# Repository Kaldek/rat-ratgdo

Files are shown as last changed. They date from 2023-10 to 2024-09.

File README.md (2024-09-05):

# rat-ratgdo
RAGE
AGAINST
THE
RATGDO



Credit and inspiration for this work goes to [@rlowens](https://github.com/rlowens) to let me know that there are other technical folks out there who needed this other than myself.

## Overview
This is an open source schematic for the ratgdo, based on the v2.5 [ratgdo](https://github.com/PaulWieland/ratgdo) PCB and code but installed using the [ESPHome fork](ESPHome%20vs%20native%20ratgdo.md) of ratgdo.  This project was created to allow people who need a ratgdo solution for their garage door opener but either cannot, or choose not to, source the solution from Paul Wieland. It also ensures that the PCB can be recreated as and when the project maintainer gives up on the project (much like Chamberlain themselves might do with their MyQ Cloud Service) and stops selling PCBs. 

### You are expected to know how to create the described circuit using your own prototyping skills.  That is, this project is for people who can solder well and know how to read schematics

The ***basic*** PCB schematic shown here in the Readme does not describe any circuitry other than the serial line garage door control and obstruction sensor.  All other optional features provided by ratgdo can be reverse engineered as needed, or may already be solved by one of the schematics the community has uploaded!

 As of January 2023, there are now multiple sources for commercially sold ratgdo boards.  **However if you want to buy a pre-made ratgdo setup, we recommend purchasing one [from Paul Wieland](https://github.com/PaulWieland/ratgdo) so as to reward the original creator.**

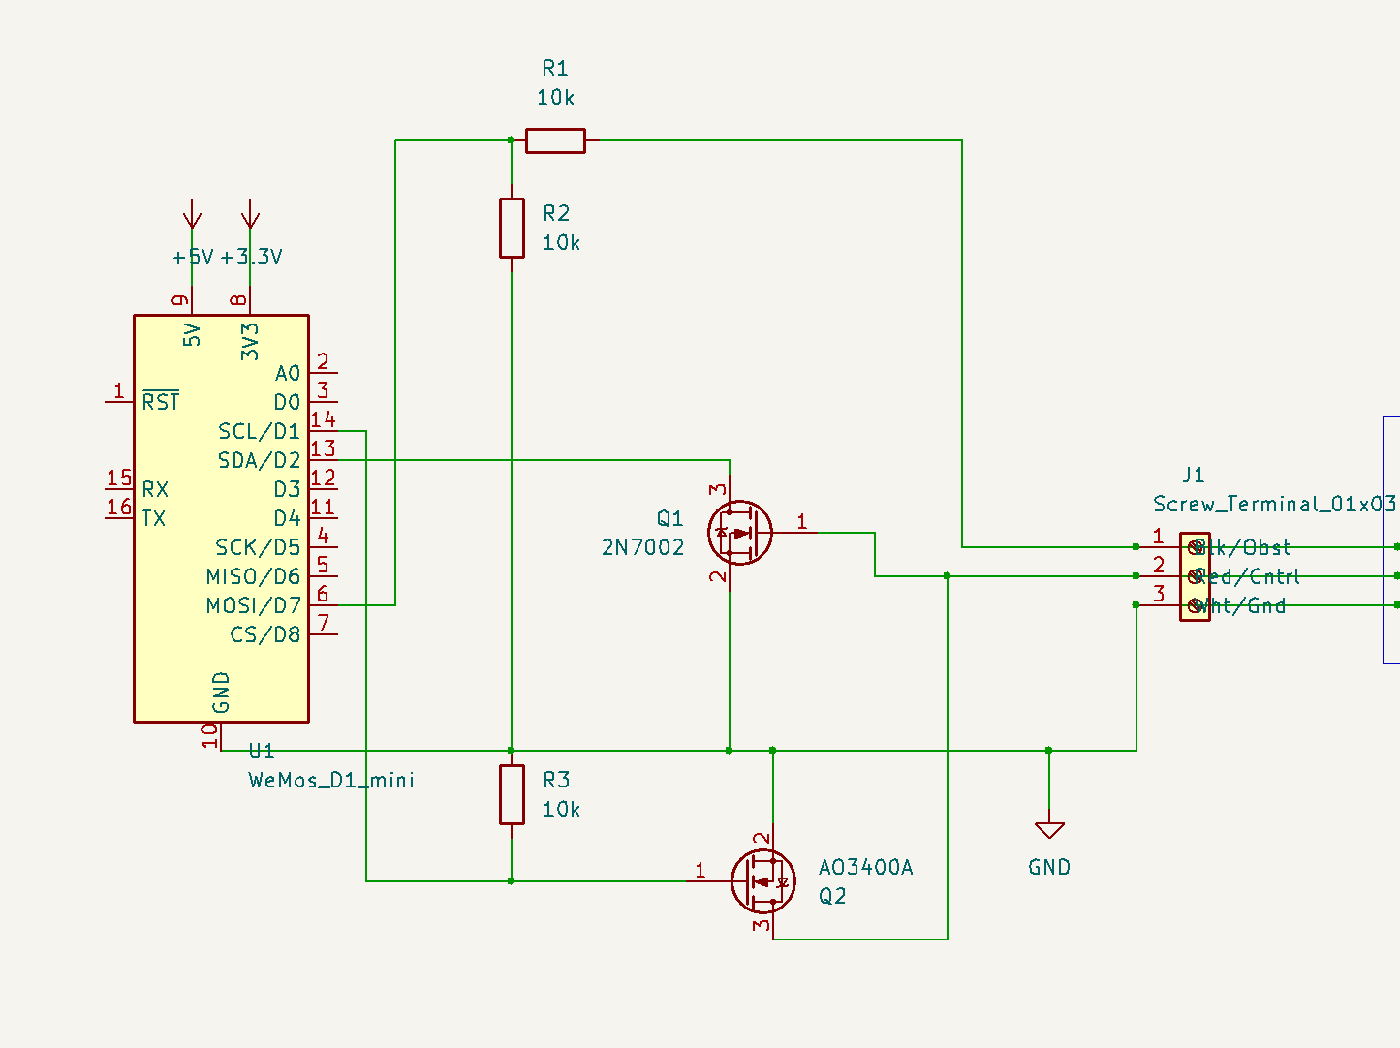
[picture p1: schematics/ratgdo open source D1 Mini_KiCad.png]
PCB Link

_Simple basic schematic for a Wemos D1 Mini based module_

See images of a [working breadboard prototype](images/Breadboard_working.png) and the [subsequent soldered prototype using a D1 shield](images/Simple%20prototype%20using%20D1%20shield.jpg).  Both of these prototypes are using 2n7000 MOSFETs exclusively, but that is because they are prototypes and whether a 2n7000 will work for TX will depend greatly on who manufactured your 2n7000.  See the section below on needed components for context.

## Components needed for basic functionality
The basic schematic shown above assumes the use of through-hole components.  If you wish to use SMD components, please refer to the [FAQ](FAQ.md#what-if-i-want-to-use-sot-23-smd-components), and you can also check out the community-provided schematics, which include SMD-based designs.

For this basic design, aside from the obvious requirement of a [supported ESP-32 or ESP8266 board](Supported%20Boards.md) flashed with the [ESPHome version](https://github.com/ratgdo/esphome-ratgdo), you will need:
- 3x 10 kohm (kilo-ohm) resistors
- 1x 2n7000 MOSFET for the RX pin
- 1x AO3400A (soldered to a SOT23 to DIP adapter board) for the TX pin.

It is also recommended you aquire a suitable 3-post screw terminal and some red, white, and black wire for connecting to the door opener.  These connections are very low current, so you can get away with fairly thin wire.

**Note:**  You may **try** to use a 2n7000 MOSFETs for **both** RX and TX, however depending on the manufacturere of your 2n7000 and its production batch, it might not be 100% reliable for the TX circuit because the ~3v switching signal from the ESP8266 may not be enough to trigger the gate of the 2n7000.  There are many examples working using the 2n7000 however, so it might work.  If you have reliability issues for sending commands, we can only recommend you use the AO3400A SMD MOSFET, soldered to a SOT23-to-DIP adapter board.  

## INSTALL REQUIREMENTS
For both this basic schematic shown here in the Readme and how they it is laid out, you must use the ESPHome fork of ratgdo and - for ESP8266 based boards - select the "ratgdo v2.5x" image on the ESPhome [web installer page](https://ratgdo.github.io/esphome-ratgdo/).  For ESP32 based boards the above does not currently apply and you must use the v2.0 installer and follow our basic ESP-32 schematic we provide in the Supported Boards page.

For the ESP8266 based boards, if installing using Paul Wieland's native ratgdo installer and you install for a v2.0 board, you must wire your TX to D4 (GPIO2) rather than D1 (GPIO5).

## Having a PCB printed
You may use the files from the [schematics folder](kicad_files) to have your own PCB printed.  Shown is an example 3D render of an ESP32 based board using a Wemos ESP32 D1 board.

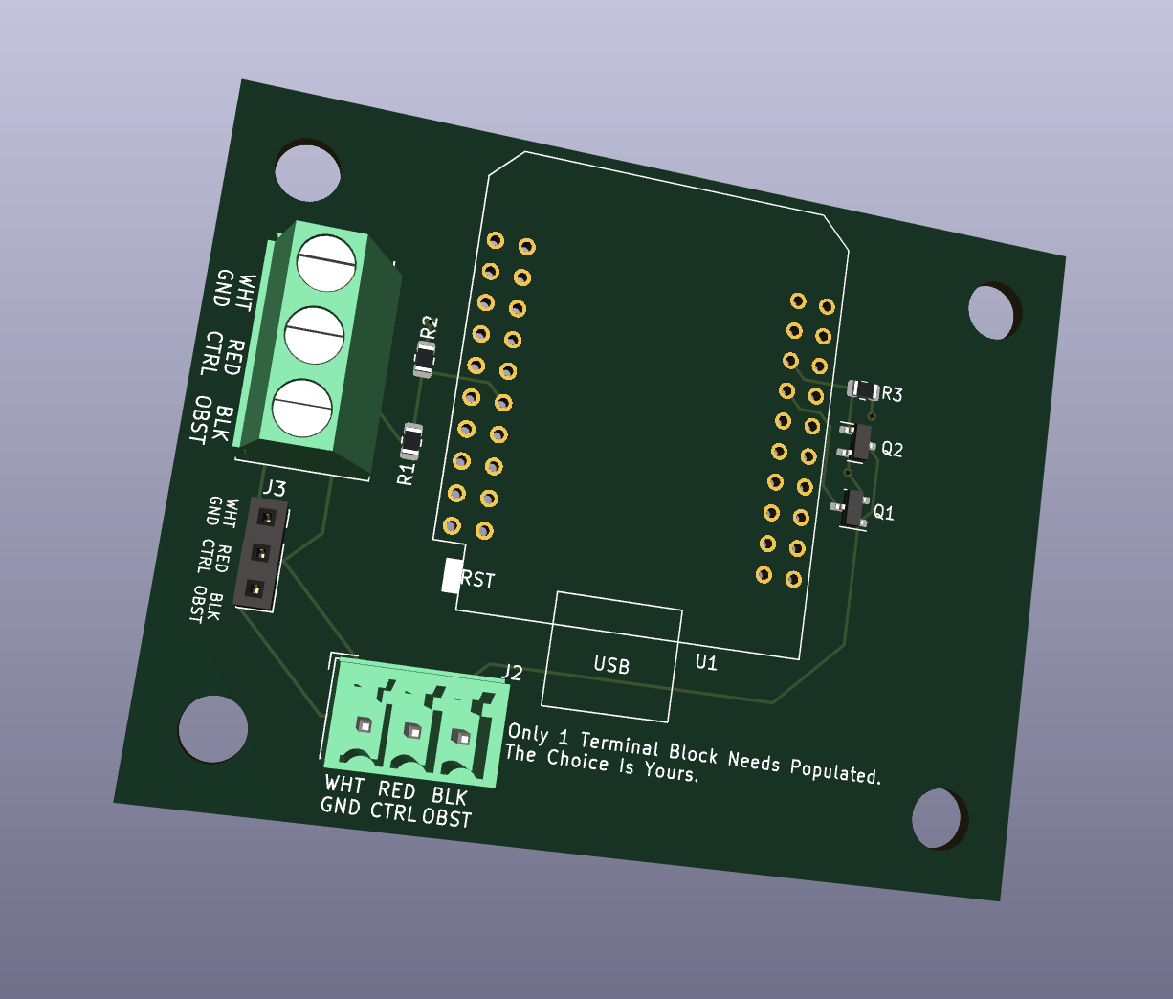
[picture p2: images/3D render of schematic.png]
3D render of printed PCB

_An example of the D1 Mini ESP32 Wide Format_

Here is an example of a printed PCB with a raw ESP8266 and an LM2596 module, for being powered by a GDO with the battery backup capabilities.
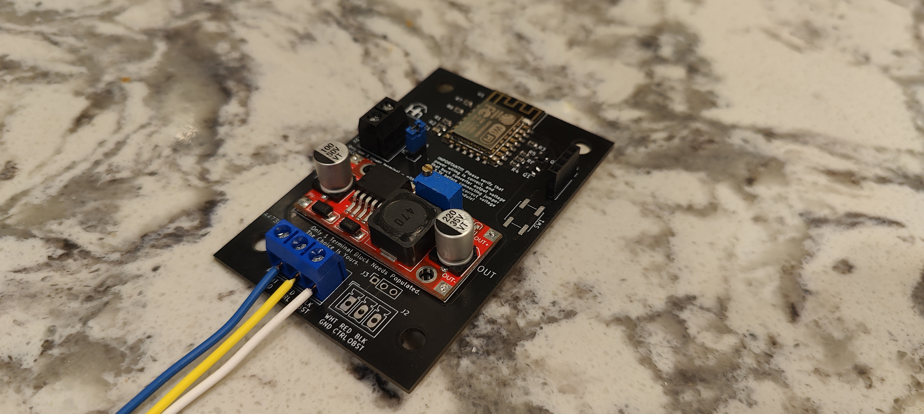
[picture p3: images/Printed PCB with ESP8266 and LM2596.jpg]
Printed PCB using ESP8266 and LM2596

_An example of a PCB using a bare ESP8266 and LM2596 module_

### Schematic options
The community has provided a few options of schematic files suitable for sending to a PCB printing company.
- [Wemos D1 Mini ESP8266](kicad_files/D1%20Mini%20-%20ESP8266)
- [Wemos D1 Mini ESP32](kicad_files/D1%20Mini%20-%20ESP32) (massive overkill for ratgdo but it's your choice!)
- [Wemos D1 Mini ESP32 Wide Format](kicad_files/D1%20Mini%20Wide%20-%20ESP32)
- [Bare ESP8266 module](kicad_files/Bare%20ESP8266)

> If you just want to try ordering a board from somewhere like PCBWay, then check out the most recent [build artifacts](https://github.com/Kaldek/rat-ratgdo/actions/workflows/pcb.yaml)

## How the ratgdo circuit works
The ratgdo circuitry which we cover in this project consists of two sections; Garage Door control and obstruction sensors.

### Garage Door Control
#### Description of the Chamberlain configuration
The Chamberlain garage door control circuit is a two-wire setup consisting of a Ground, and a combined +12v power and serial data line.  The serial data line is held at 12v unless data transmission is occurring.  Data transmission is performed by pulling the 12v line down to GND for each data bit.  The benefit here is that a single wire can be used for providing power to door control panels and data transmssion on a single wire.  The use of appropriately sized capacitors in door control panels means they do not switch off during data transmission.

#### How ratgdo interfaces with the Chamberlain wiring
The ratgdo taps into the red control wire and uses this single wire for transmission of commands onto the serial bus, and for receiving data from the serial bus.  As it is a single wire protocol and operates half-duplex, the ratgdo circuitry uses N-channel MOSFETs wired in a manner which allows the ESP8266 to never transmit when the serial line is already low.

In operation, this means that the ratgdo is mostly listening to the serial bus to ensure it is keeping track of the state of the door.  For example, if the door is manually opened (or opened by use of the MyQ app even), these events are broadcast onto the serial bus by the door controller.  ratgdo is therefore able to know that the state of the door has changed.  In turn, this means that when controlling ratgdo via Home Assistant, the status of the door in HA is always up to date.

#### Wiring to Garage Door


### Obstruction sensor
The ratgdo monitors the real-time state of the obstruction sensors directly.  We assume this is because obstruction status is not broadcast in real time by the door controller, and safety is paramount.  It allows you to set up real-time alerts in Home Assistant for any time the door is obstructed.  The ratgdo taps into the obstruction sensor power wire which also acts as a communication bus, however the signalling is only an ongoing status of whether the obstruction sensors are working and whether there is an obstruction.

## Contributing
This is a fully open repo, in that we welcome any and all additions for all sorts of Edge Cases.  If you come up with something and would like it to be available to the community, raise a Pull Request and we'll work with you to get it published!

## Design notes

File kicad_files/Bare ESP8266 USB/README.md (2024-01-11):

# ESP8266 12-F USB-C KiCad files

A reworking of the Bare ESP8266 board design that uses USB-C for power instead of an LM2596 submodule, and uses just one GDO connector header to allow for a smaller board footprint.

Compatable with RatGDO ESPHome software for the v2.5 official board.

## Populating

Populating the Flash switch, Reset switch, and ICSP header are optional, but will make first time programming easier.

## Powering 

This board uses a 6-pin power-only USB-C jack that can be either hand soldered or paste reflowed. It's a normal 5V USB sink device, so any "dumb" USB wall-wart can be used.

It can also be powered via the 3.3V pin of the ICSP header - there's no need to connect USB while serial programming it.

If you wish to power the device directly from the programming header using 3.3V, you can skip populating the USB-C port, resistors R2 and R3, and the LDO regulator CR1, but you should ensure you're using a stable and regulated 3.3V supply.

If your GDO has battery backup system, I'd recommend using one of the LM2996 module based boards in this repository instead of this one.

## Programming

The USB-C port on this board is for power only - you need to use the ICSP programming header with a seperate TTL-level RS232 programming interface to load the initial firmware.

The ICSP header will mate directly with the 
[SparkFun Serial Basic Breakout](https://www.sparkfun.com/products/14050) for programming, but any 3.3V RS232 interface can be used by connecting TX, RX, VCC and GND appropriately.

Auto reset via serial hardware control lines isn't supported - you'll need to press the Reset button manually after programming, or power cycle the device.

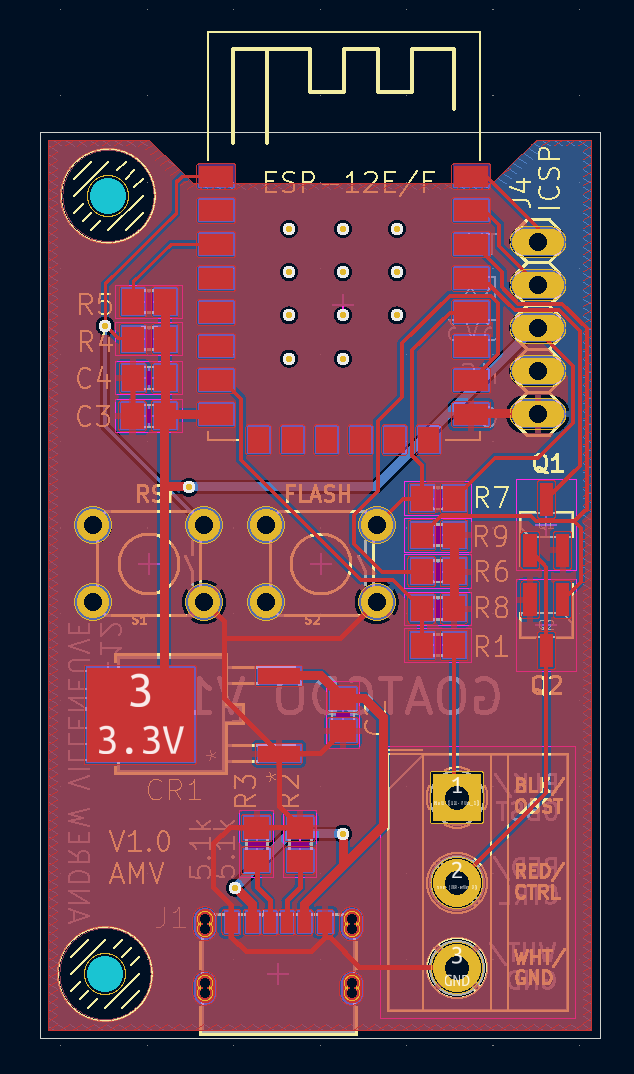
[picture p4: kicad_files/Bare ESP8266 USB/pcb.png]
KiCad Board View

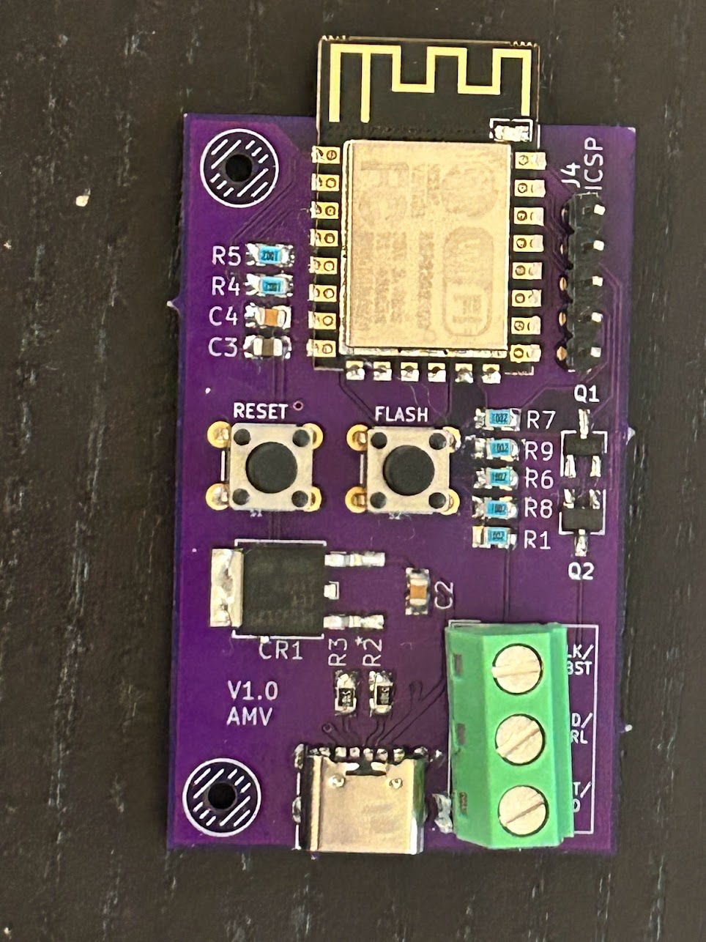
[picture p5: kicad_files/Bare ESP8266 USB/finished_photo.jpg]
Populated Board


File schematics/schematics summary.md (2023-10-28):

Place all schematic files and images here.

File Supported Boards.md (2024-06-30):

## ESP8266 D1 Mini boards
All ESP8266-based D1 Mini boards are supported, and are the hardware which the ratgdo project uses for the pre-made kits available from Paul Wieland.

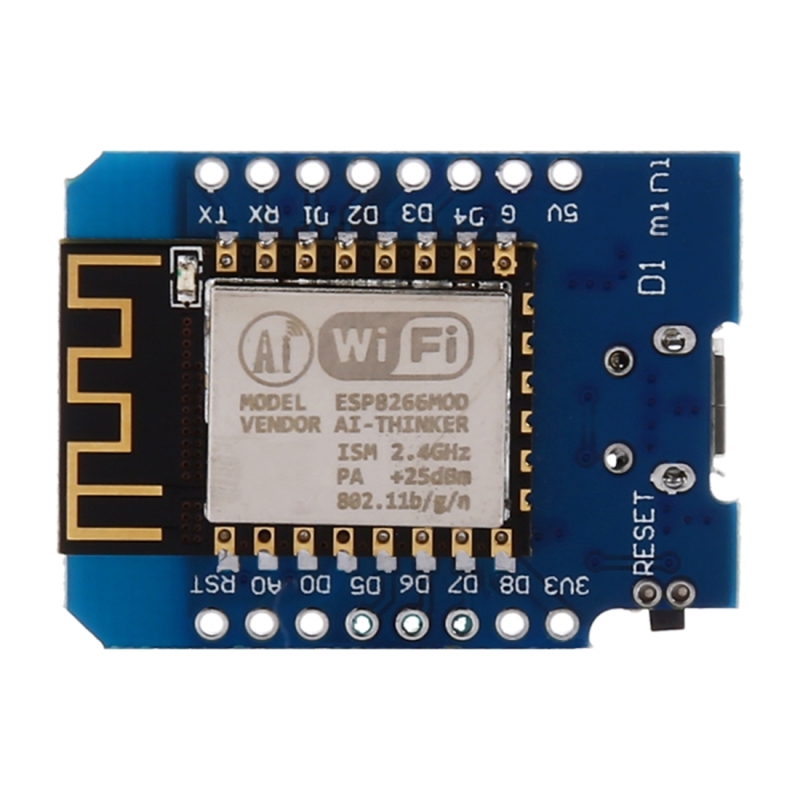
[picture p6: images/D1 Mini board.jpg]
D1 Mini Board


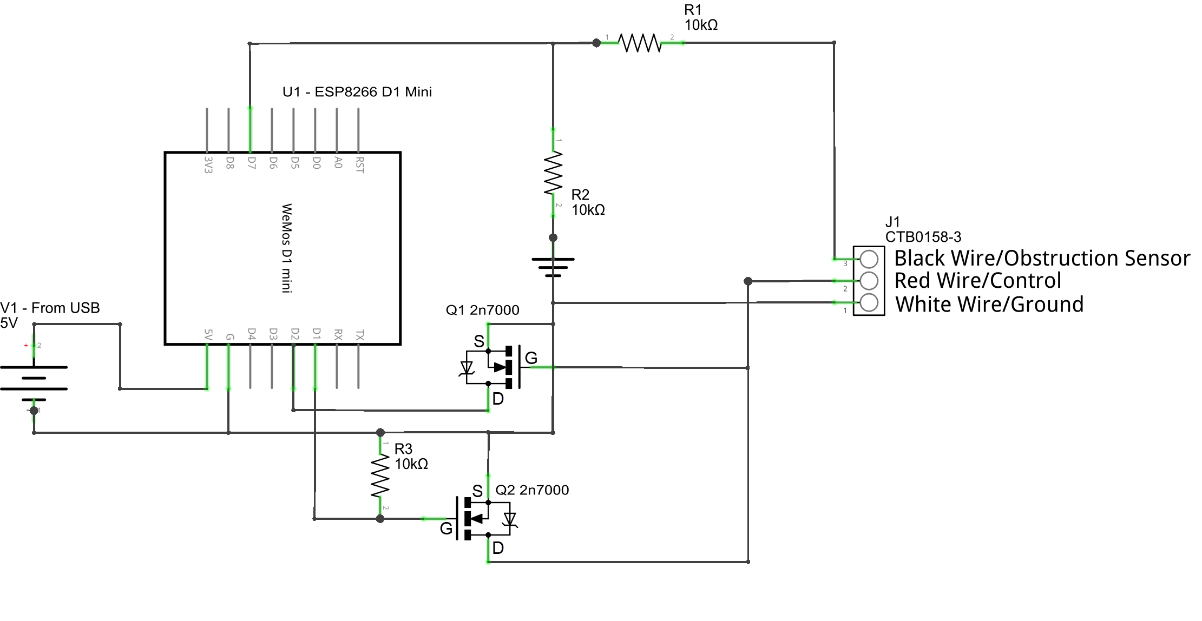
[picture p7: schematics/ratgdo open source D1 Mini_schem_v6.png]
ESP8266 D1 Mini Schematic


Note that the D1 Mini **module** takes 5v and an on-board regulator drops this down to the 3.3v power used by the ESP8266 chip.

## ESP-32 based boards
All ESP-32 boards are directly supported by the ESPHome Ratgdo port, using the [ESP32 D1 Mini YAML file for install settings for a version 2.0 ratgdo board](https://github.com/ratgdo/esphome-ratgdo/blob/main/static/v2board_esp32_d1_mini.yaml).

**CRITICAL**: You must install using the v2.0 install for ESP-32 boards as v2.5 is additional and unnecessary work for these boards at the current time.

**Note:** The pin numbers mentioned in the linked YAML file are only directly valid for the D1 Mini ESP32 boards.  Regardless of ESP-32 board used, these are the **actual** ESP-32 pins used for v2.0:
| ratgdo function | ESP-32 pin |
| --- | --- |
| TX | GPIO16 |
| RX | GPIO21 |
| Obstruction | GPIO23 |
| White/GND | GND |

For your particular board, you may need to determine which board traces map to these GPIO pins.

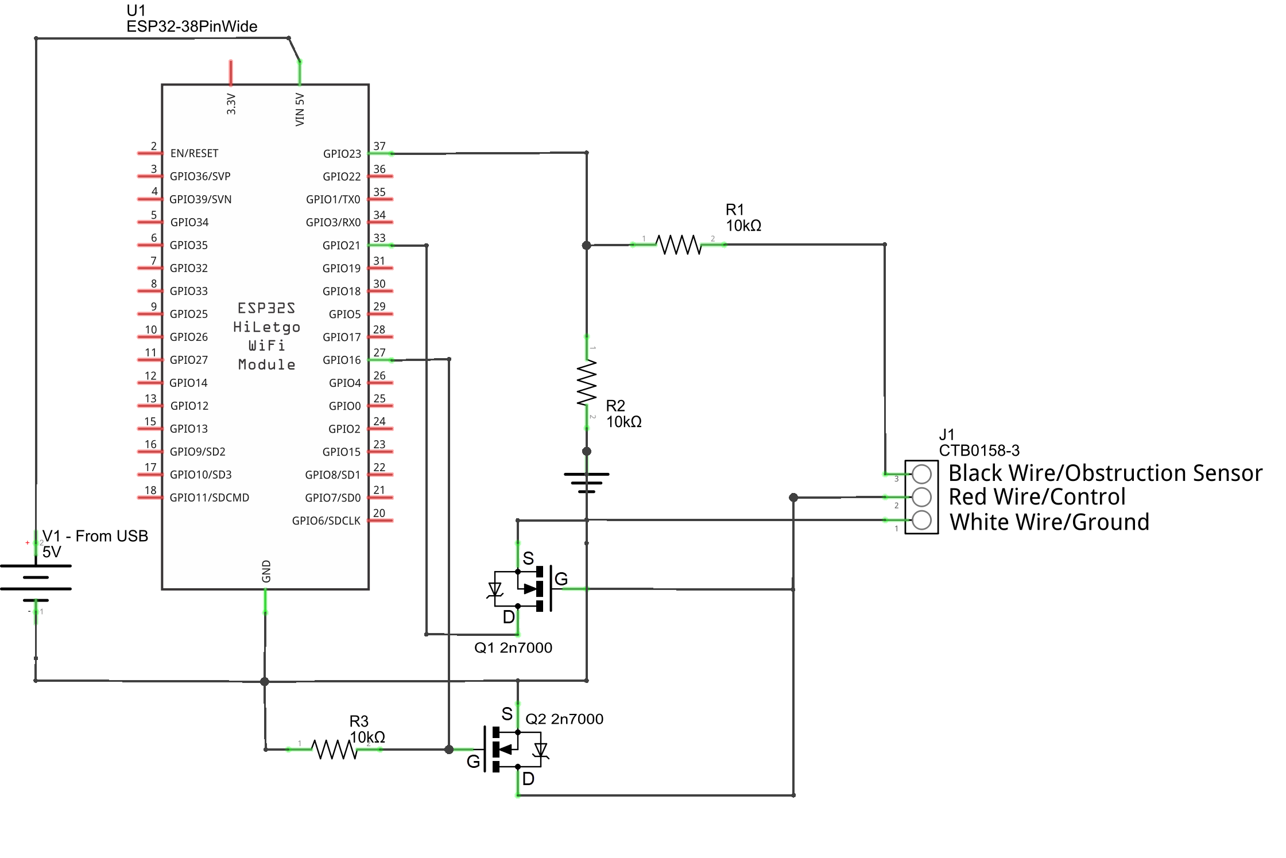
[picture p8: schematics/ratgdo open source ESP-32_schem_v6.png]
Generic ESP-32 board pinout


Note that ESP-32 **modules** take 5v power from USB and an on-board regulator drops this down to the 3.3v used by the ESP-32 chip.

### ESP-32 D1 Mini boards
Supported by the ESPHome Ratgdo port, using the ESP32 D1 Mini YAML file for install settings, noting thepinout mappings below..  Note that the outer row of pins on the D1 Mini board are not used for ratgdo.

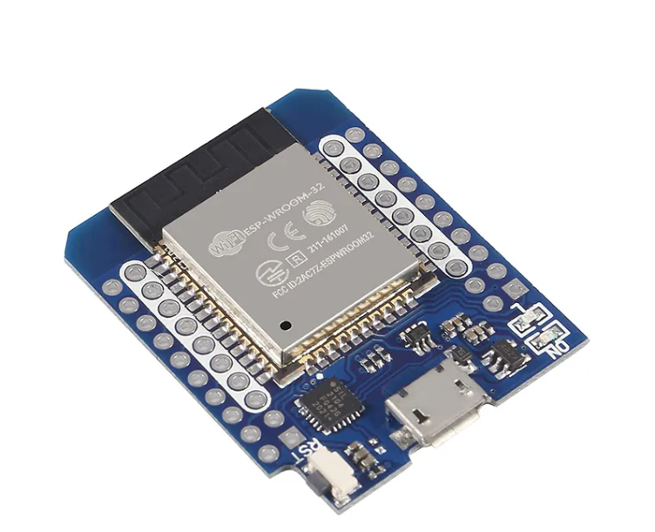
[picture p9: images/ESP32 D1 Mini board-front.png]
ESP-32 D1 Mini Front view

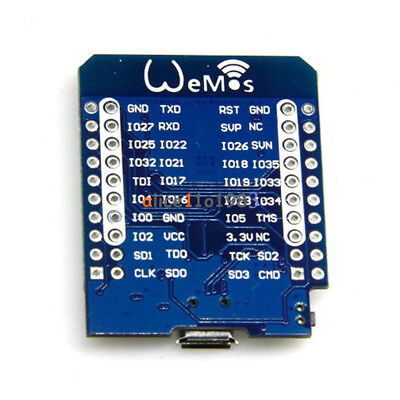
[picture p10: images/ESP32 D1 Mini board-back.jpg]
ESP-31 D1 Mini back view


GPIO pins for the ESP-32 D1 Mini are as follows:
- TX: IO16
- RX: IO21
- Obstruction: IO23

### ESP-WROOM-32
Supported by the ESPHome Ratgdo port, using the ESP32 D1 Mini YAML file for install settings, noting thepinout mappings below.

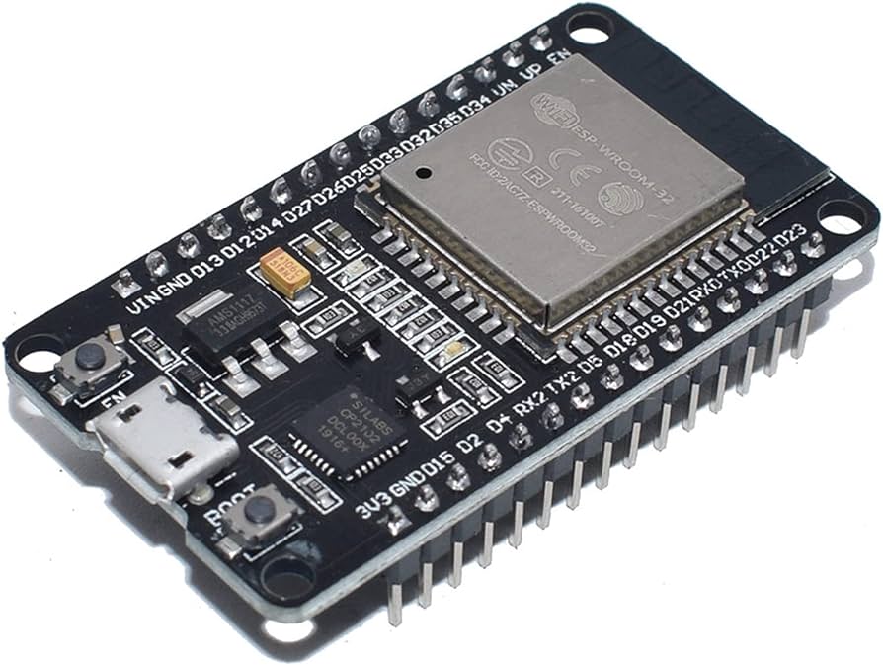
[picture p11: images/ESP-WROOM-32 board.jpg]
ESP-WROOM-32 board


GPIO pins for the ESP-WROOM-32 are as follows:
- TX: RX2
- RX: D21
- Obstruction: D23

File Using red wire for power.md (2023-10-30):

# Prototype notes for powering ESP module
We are testing use of an LM2596 voltage regulator (buck converter) module to power the ESP without needing a separate USB power supply.  

## Can we use the red wire to power the ESP?
Testing using this method has failed.  The LM2596 and ESP8266 combined draw too much current from the red wire for the ESP to be powered from the E-Serial lines of the Chamberlain/MyQ GDO. 

## Using the GDO Battery Backup connector to power the ratgdo
GDO models that are compatible with the Standby Battery Power System (e.g., the PN 475LM, [disassembly video](https://www.youtube.com/watch?v=qWsHb-kiO6w)) or have one built-in, can use the same 2-pin connector to power their LM2596 module.  Just be sure that you first adjust the output of your LM2596 voltage regulator to 5v **before** you connect it to your ESP **module**.  More information on the connector can be found in [this thread](https://www.garagejournal.com/forum/threads/battery-backuo-connector-for-liftmaster-8500-garage-door-opener.514321/).

### Overview of module setup
One of the many common pre-built LM2596 voltage regulator modules can be used, either as unit pre-set to 5v output or an adjustable unit that has been set to output 5 volts.

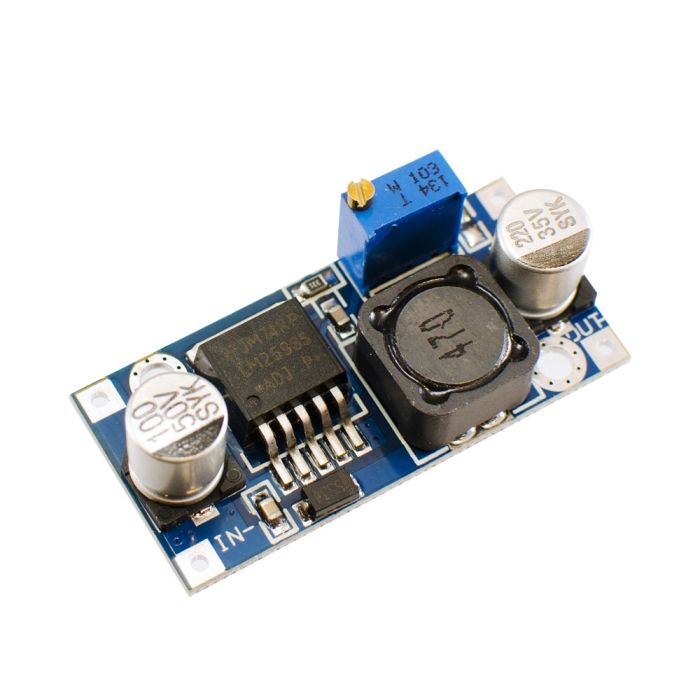
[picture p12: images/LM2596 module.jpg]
LM2596 module example


### Pinouts

Pinouts are planned as follows for using the Battery Backup terminals on the GDO:
| LM2596 Module Pin | Garage Door Opener wires |
| :--- | :--- |
| IN+ | Battery Backup Positive terminal |
| IN- | Battery Backup Negative terminal |
| OUT+  (5v) | ESP Module 5v |
| OUT- | ESP Module GND |

#### Why 5v output and not 3.3v?
If using an ESP ***module*** these have an onboard 5v to 3.3v voltage regulator and do not expose a 3.3v "in" on their connectors.  3.3v would only be used if you are powering a "naked" ESP8266.

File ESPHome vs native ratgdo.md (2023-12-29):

# Why we recommend ESPHome
Paul Wieland is the original creator of the ratgdo project and deserves all credit for its creation. However, when using custom schematics and PCBs, the ESPHome fork of ratgdo is more suitable.

The benefits of using ESPHome are:
- Web interface provides better out of the box diagnostic and logging
- Pins used for ratgdo functions can be altered without coding expertise
- ESPHome automatic discovery
- Easy support for 4MB Flash ESP8266 modules, allowing for OTA updates via ESPHome Add-On in HA

## Web interface benefits
The ESPHome web interface provides full details on a single web page of all current states of the ratgdo data in real time.  It also provides a realtime console log and, if you access the web page early enought in the boot cycle of the ESP8266, you can see the hardware settings that have been applied.

[Example of ESPHome Web GUI](https://github.com/Kaldek/rat-ratgdo/blob/main/images/ESPHome%20Web%20Gui%20example.png)

## Custom Pins for ratgdo functions
The ESPHome fork of ratgdo allows you to edit configuration settings for the ratgdo device in a YAML file on your Home Assistant (HA) server.  This includes the GPIO pins that will be used for obstruction detection, TX, RX, and the dry contacts.  ESPHome will then perform an on-the-fly recompile of the ESPHome and ratgdo binary and push these settings to the ESP module **Over The Air**.

Note that this requires installation of the ESPHome Add-On to Home Assistant.

## ESPHome Automatic Discovery
Any devices on the network using ESPHome will advertise their presence on the local network.  This **includes** using Multicast DNS (MDNS) which means that if you have a suitable MDNS forwarder (such as the [avahi deaemon](https://www.avahi.org/) at https://www.avahi.org/) and your ratgdo is on a separate IP subnet, it will still be detected by Home Assistant.  Handy for those of us who segment our "IoT" networks.

ESPHome Automatic Discovery and registration into Home Assistant does not require the ESPHome Add-On.  The Add-On is required for advanced functions like the customised YAML files as mentioned above.

Automatic regestration also correctly registers the ratgdo in Home Assistant as a garage door without any further work.

## ESPHome OTA support for 4MB flash modules
The default guidance is to use the ESPHome ratgdo YAML files for the Wemos D1 Mini Lite.  As a result, ESPHome will assume your device has 1MB Flash even if it has 4MB (e.g., Wemos D1 Mini has 4MB Flash whereas the Wemos D1 Mini Lite only has 1MB).

ESPHome added support for modules with 4MB flash via support for the 2.5i version of Paul Wieland's ratgdo product, which includes an ESP-12F module that has 4MB flash.  If your module has 4MB flash, just select the v2.5i board when installing ESPHome.

### Initial re-flash after updating YAML
If you are re-flashging an existing deployment of ESPHome-ratgdo for your module with 4MB flash, you will initially need to re-flash your module either using USB or via stripping out all of the ratgdo references from the YAML so that the OTA file fits in the remaining spare flash space.  This is because that the change to your YAML only effectively applies after one successful installation of the YAML with the reference to the d1_mini.

## ESPHome OTA support for 2MB flash modules
Currently the esphome-ratgdo repository does not directly support configurations for ESP8266 modules with 2MB flash (such as the Tuya TYWE3L and TYWE3S), as the list of modules supported in their provided YAML files reference the "D" pin numbering of Wemos modules.  These modules will work with any configurations for modules with 1MB flash though.

We have forked the esphome-ratgdo repository, and provide unofficial support for 2MB modules via the following device YAML you can use in the ESPHome Dashboard:

```yaml
substitutions:
  name: ratgdov25-2MB
  friendly_name: RAT-RATGDO-2MB
  id_prefix: ratratgdov25

packages:
  ratratgdo.esphome:
    url: https://github.com/Kaldek/esphome-ratgdo
    ref: main
    file: rat-ratgdo-2MB.yaml

esphome:
  name: ${name}
  name_add_mac_suffix: false
  friendly_name: ${friendly_name}
```

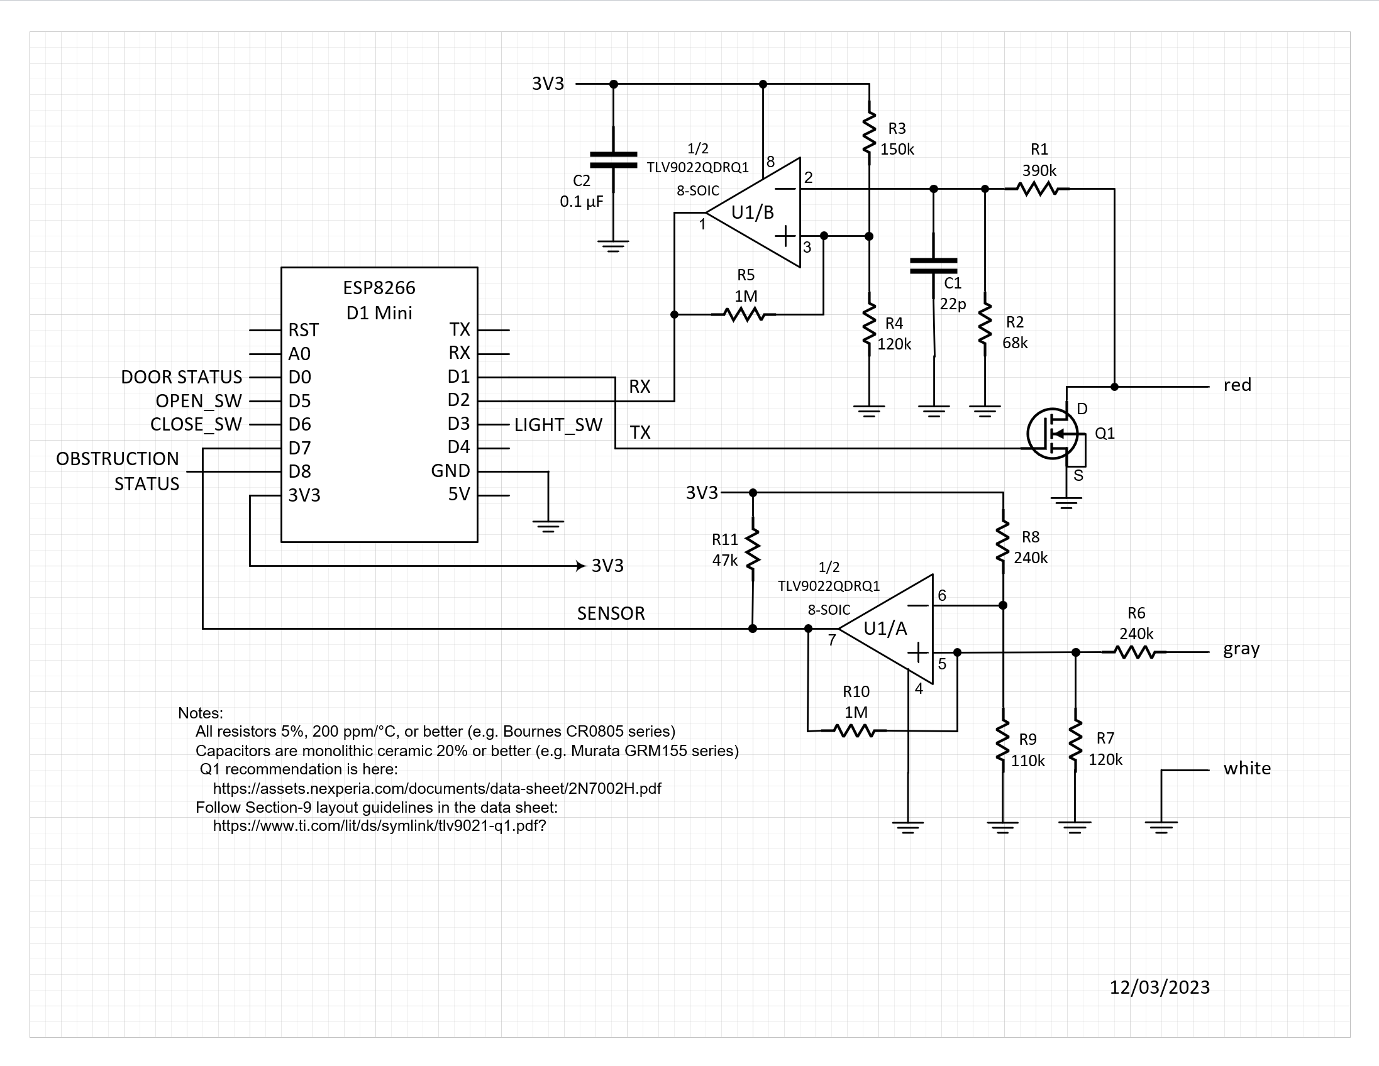
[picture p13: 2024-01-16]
schematics/Alternate_interface_design.png

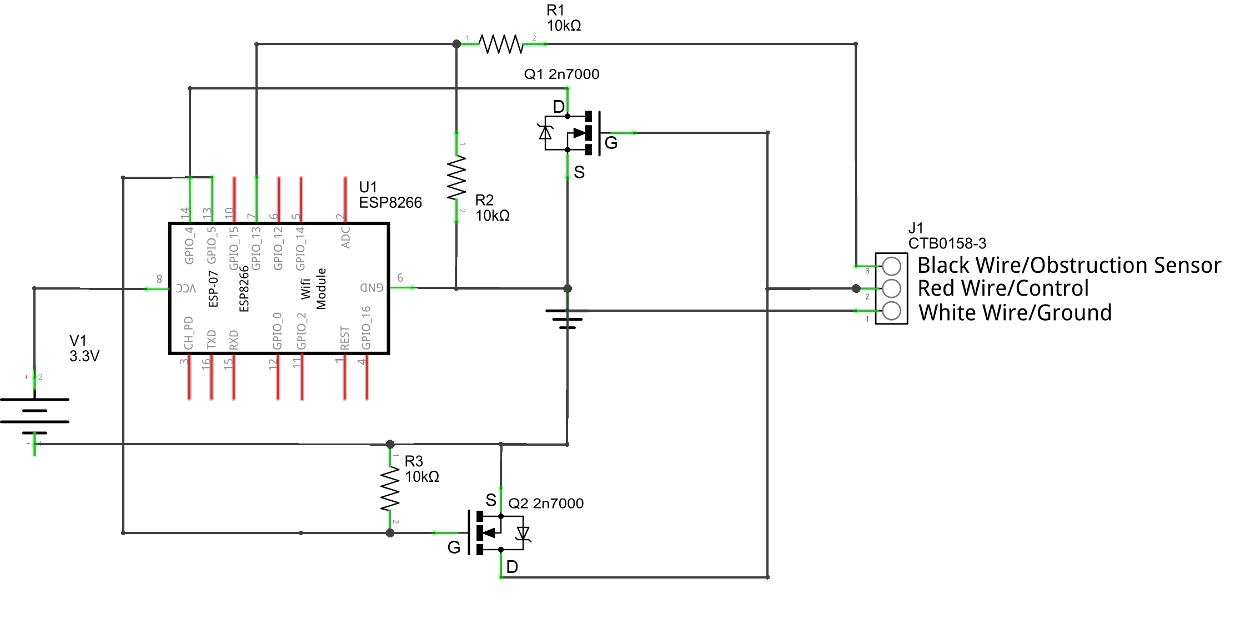
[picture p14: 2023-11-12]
schematics/ratgdo open source_schem_v9.png

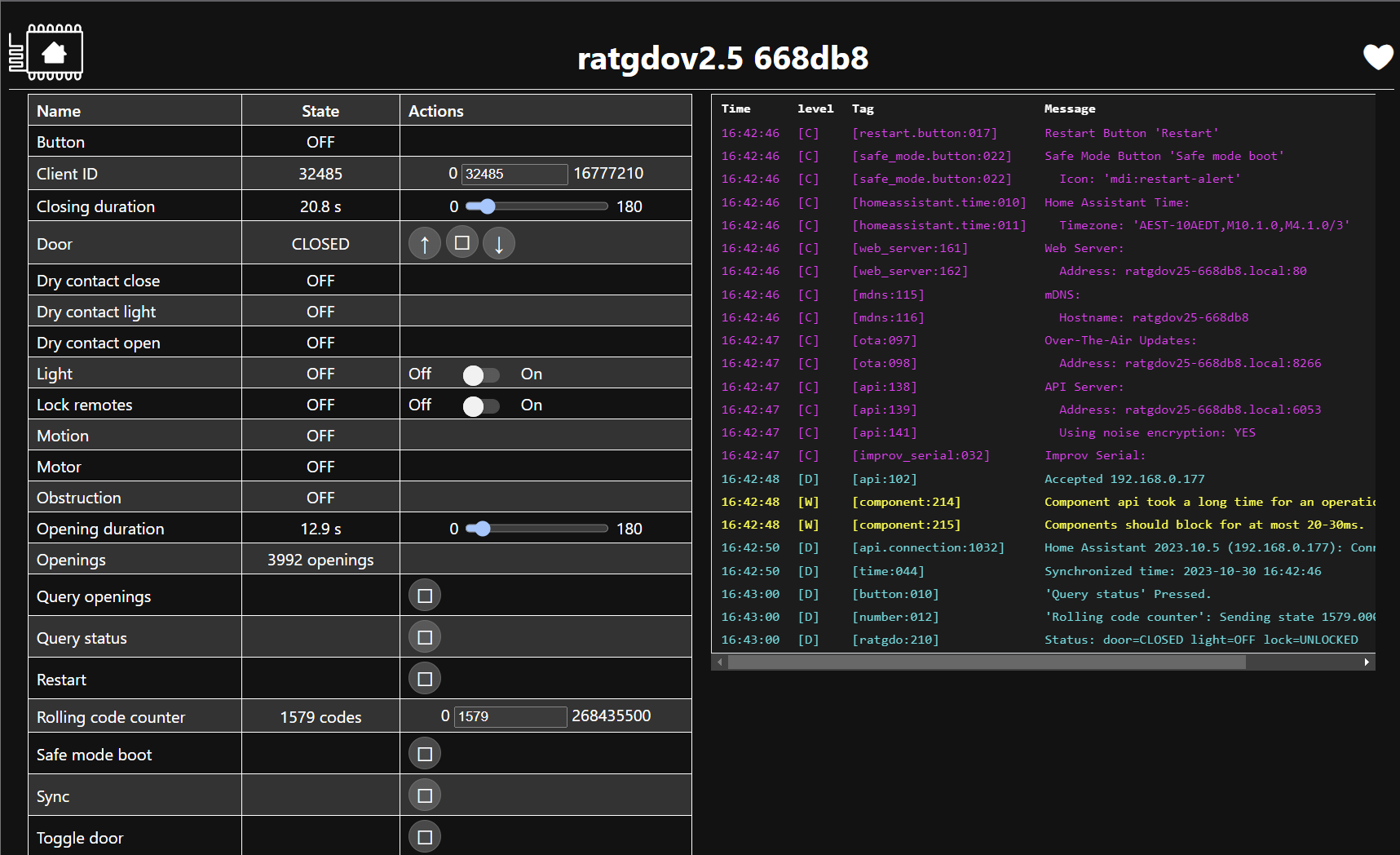
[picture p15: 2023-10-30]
images/ESPHome Web Gui example.png

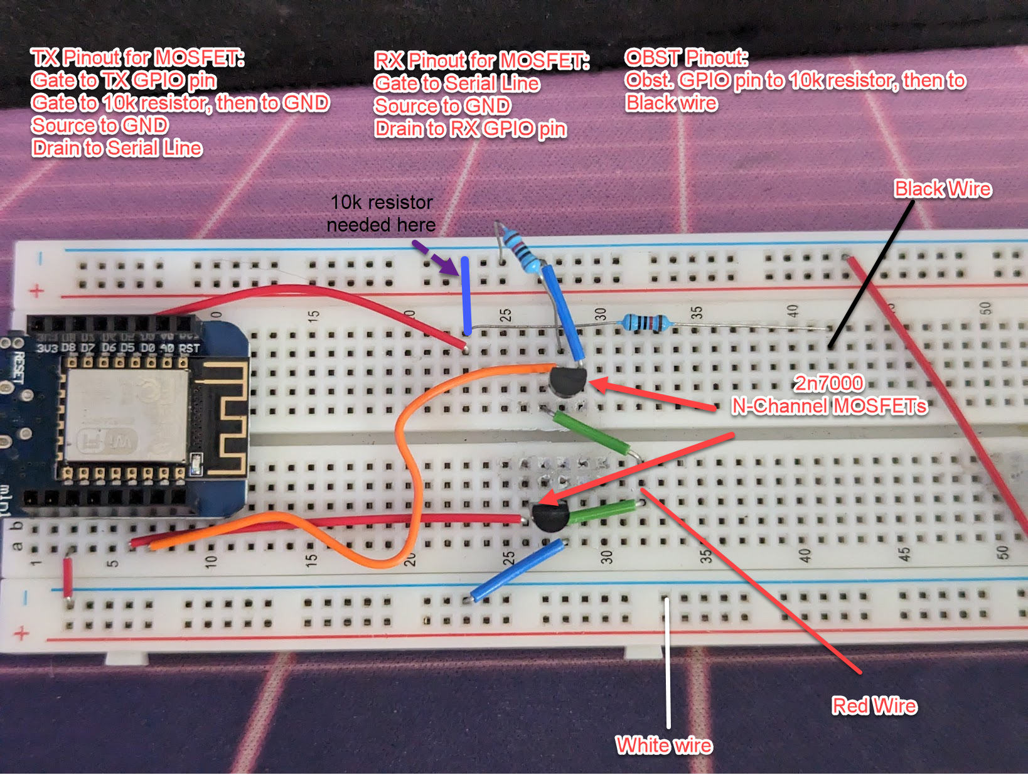
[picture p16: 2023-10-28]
images/Breadboard_working.png

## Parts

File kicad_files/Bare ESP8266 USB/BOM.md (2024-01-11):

## BOM

|Part 	|Qty 	|Value 	|Reference 	|Link 	|
|-|-|-|-|-|
|0805 Resistor 				|7 	|10k 	|R1, R4, R5, R6, R7, R8, R9 	|																											|
|0805 Resistor 				|2 	|5.1k 	|R2, R3 						|																											|
|0805 Capacitor				|2 	|100nF 	|C2, C4 						|																											|
|0805 Capacitor				|1 	|10uF	|C3 							| 																											|
|Switch (Optinal) 			|2 	| 		|S1 (Rst), S2 (Flash)			|[Digikey](https://www.digikey.com/en/products/detail/cui-devices/TS02-66-60-BK-100-LCR-D/15634327) 		|
|2N7002 					|1 	| 		|Q1 							|[Digikey](https://www.digikey.com/en/products/detail/onsemi/2N7002/244345) 								|
|AO3400A 					|1 	| 		|Q2 							|[Digikey](https://www.digikey.com/en/products/detail/alpha-omega-semiconductor-inc/AOSS32334C/11567443)	|
|2.54mm header (Optional)	|1 	| 		|J4 (ICSP)						| 																											|
|1x3 Screw Term				|1 	|		|J2	(GDO)						|[Digikey](https://www.digikey.com/en/products/detail/phoenix-contact/1729021/260605)						|
|3.3V LDO Regulator			|1 	|LD1117 |CR1 							|[Digikey](https://www.digikey.com/en/products/detail/stmicroelectronics/LD1117ADT33TR/669253) 				|
|ESP8266 12F 				|1 	|		|IC3 							|[Amazon](https://www.amazon.com/gp/product/B089PTN2V5/) 													|
|USB-C Connector			|1 	|		|J1 							|[Digikey](https://www.digikey.com/en/products/detail/kycon-inc/KUSBX-SMT-CS-6-BTR/13545035)				|

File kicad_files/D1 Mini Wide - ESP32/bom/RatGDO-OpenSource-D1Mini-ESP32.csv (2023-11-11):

Id | Designator | Footprint | Quantity | Designation | Supplier and ref
1 | U1 | ESP32_mini | 1 | mini_esp32
2 | R3,R2,R1 | R_0805_2012Metric | 3 | 10k
3 | J3 | PinSocket_1x03_P2.54mm_Vertical | 1 | Screw_Terminal_01x03
4 | Q2 | SOT-23 | 1 | AO3400A
5 | Q1 | SOT-23 | 1 | 2N7002
6 | J2 | PhoenixContact_MCV_1,5_3-G-3.5_1x03_P3.50mm_Vertical | 1 | Screw_Terminal_01x03
7 | J1 | TerminalBlock_Phoenix_MKDS-1,5-3_1x03_P5.00mm_Horizontal | 1 | Screw_Terminal_01x03

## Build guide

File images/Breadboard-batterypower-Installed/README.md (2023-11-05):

## ratgdo powered from battery backup using Linear voltage regulator
It is possible to use a linear voltage regulator rather than a buck converter module to provide 5v for ESP boards that have an onboard 5v-3.3v voltage regulator.
<br>


## Technical description
To provide 5v power to the ESP module a linear voltage regulator (L7805CV 5V regulator) was used, coupled with filtering capacitors on the input and output sides of the regulator (100uF cap on the input, 10uf electrolytic and .1uF ceramic on the output).  The 7805 can handle 7-36v and is suitable for use in droping the voltage down to 5v for the ESP modules.

The example shown uses vampire clips to connect to the 12v wiring of the battery backup circuit


The full install is shown here.


  
<br>

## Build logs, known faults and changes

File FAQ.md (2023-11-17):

# FAQ

## Low Level Circuitry stuff
### How does the "Red Wire" on these Garage Door Openers work?
Each Garage Door Opener has two wires which connect between the GDO and any wired door control panels (the smart panels with displays and menu controls on them).  These are a +12v wire and a Ground so that DC power is provided to the control panel.

However, that same +12v wire is **also** the data line which carries data between the GDO and the control panel.  This works because each serial data pulse is a brief "pull to ground" of that +12v line.  These pulses can be read by the door control panel (and, indeed read by the GDO if the data transmission is coming from the control panel and being sent to control the door).  This is how the ratgdo both receives and transmits data as well.  In essence, it appears to be just one more control device on the "bus".

Chamberlain often refers to this combined +12v and data line as "E-Serial":
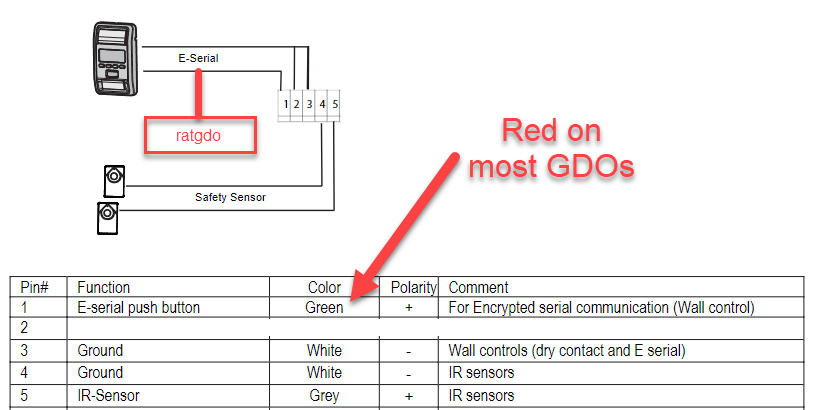
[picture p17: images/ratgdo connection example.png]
ratgdo connection example


### If the +12V line is constantly pulsed low during data transmission, how come the door control panel doesn't turn off?
There's two answers to this and both are simple:
- The data transmission is actually quite rare
- The door control panel either has some beefy capacitors in it or a supercapacitor.  Either way, the brief interruptions to power do not affect the control panel.

### How come the 12 volt serial line doesn't blow the ESP8266 GPIO lines?
It's fairly simple how this operates.  The really short version is that the MOSFETs are used as level shifters.

The more complex description is that the TX line 3.3v output is used to trigger the Gate of a MOSFET which grounds out the serial line, pulling it LOW.  The circuit being closed is between the +12V serial line and GND.  The GPIO pin therefore never sees 12 volts.

For the RX line, the Gate of the MOSFET on this part of the circuit is connected to the +12V serial line.  Whenever +12v is applied to the gate, it causes the +3.3v from the ESP8266 GPIO pin to be pulled to ground.  In this example, the voltage "push" (if you want to call it that) is going **from** the ESP8266 to the MOSFET and it is then switched to GND.  GPIO pins on microcontrollers are designed to handle this "pull to ground" as a means of signalling/logic control, so there's no risk of the ESP8266 cooking itself.  An important note to add to the RX circuitry is that when the door controller is transmitting data on the serial line, it is pulling the +12V line to GND.  When the +12V line is pulled to ground, this switches off the MOSFET used in the RX circuit and therefore the GPIO pin on the ESP8266 goes high.

So, regardless of what device is transmitting on the serial line (whether that is the ESP8266, the door opener itself, or a door control panel, the transmitting device pulls the +12v line to ground.

### How come the obstruction sensor circuit uses two resistors?
The obstruction sensor circuit uses two 10k resistors, one in series and one in parallel to ground.  This causes the resistors to act as a voltage divider, bringing the voltage "seen" on pin D7 (GPIO13) down to ~3.3 volts.

### What bitrate is the MyQ serial communication?
As per the code from the ratgdo project, it is 9600 bits per second.

### Could I power the ESP8266 from the +12v serial line?
Whilst this is how the MyQ wall controllers work, the ESP modules pull too much current. However if your GDO has the connectors for battery backup you can [use a voltage regulator module](https://github.com/Kaldek/rat-ratgdo/blob/main/Using%20red%20wire%20for%20power.md) to do this.

### What if I want to use SOT-23 SMD components?
If you want to use SOT-23 SMD components rather than through-hole, the following MOSFETs are recommended:
- RX line: 2N7002
- TX line: AO3400A

For resistors, knock yourself out.  Any size you like as long as it's 10 kohm.

## Higher level topics

### My GDO terminals aren't red/white/black!
Some of the Chamberlain GDOs have a slightly different colour scheme.  Check the manual for your specific model and look for potential different wiring labels.  Generally the GND wires are always white.

**WARNING!** Some GDOs have a Red terminal which has nothing to do with what ratgdo refers to as the "Red wire", but instead might be used as a dry contact switch for installing a physical door button that Toggles the door.

| Expected Wire or terminal Colour | Possible Names | Possible Colours |
| :--- | :--- | :--- |
| Red | E-Serial | Green |
| Black | IR-Sensor | Grey |

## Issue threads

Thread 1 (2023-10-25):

great work lol ive done the same. what new in the new board?

tmeredyk, 2023-10-25:
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

Kaldek, 2023-10-25:
Looks like you're using the dry contact setup, which this project doesn't cover.    What component are you using specificially for the connection between D4 and the red wire other than the 10k resistor?  Have you built and tested this?

tylermeredyk, 2023-10-25:
This is just a trace by trace copy. And all the smd labels are as they are on the board. The mosfet between the 10k labeled xoyl 4n. Is most likey a alphaomega, maybe a a03400a but I’m not 100%

tylermeredyk, 2023-10-25:
And 30$ for something like this, given the components and board design is a bit insane. Don’t you think?

CrazyCoder, 2023-10-25:
What would be the minimal schematics for the dry contact configuration mode like supported in 2.5 version? I have a stupid Genie opener and would like to DIY the board to control it. Thanks for sharing the information!

rlowens, 2023-10-25:
> What would be the minimal schematics for the dry contact configuration mode like supported in 2.5 version? I have a stupid Genie opener and would like to DIY the board to control it. Thanks for sharing the information!

I can't find the firmware source for the v2.5 Dry Contact firmware, and we haven't seen what the board looks like to trace any changes that help with the Dry Contact wiring method.  But the [wiring diagram for the v2.5 Dry Contact method](https://user-images.githubusercontent.com/4663918/277838851-e338c3bf-4eda-447a-9e79-737aa1a622a0.png) just uses the D5 Open and D6 Close dry contact inputs as limit switches, and they just have an SL 1N5819W schottky barrier diode between input and GPIO (which you can omit if you want, they are just there for extra protection). Note the warning to "Only connect obstruction sensors to ratgdio if their operating voltage is 5-7vdc!" And the [ratgdo models page](https://github.com/PaulWieland/ratgdo/wiki) mentions specifically "Genie | H8000D | Dry Contact |   | x | user accessible limit switch terminals, no obstruction sensing, voltage too high".

So you would wire up the Red Wire/Control and White Wire/Ground the same as for Security+ 1.0/2.0, wire the limit switches to D5/D6, and not connect the obstruction sensors. Then flash with the Dry Contact firmware and you should be good to go.

Let us know how it goes.

CrazyCoder, 2023-10-25:
Thanks! I also found https://github.com/PaulWieland/ratgdo/issues/145 with the discussion how to connect the obstruction sensor via the voltage divider. I'll have to check with the oscillograph how they work for my old Genie model. If they send pulses that are detected by the current algorithm, it should be possible to make them work.

There is 2.5 firmware for the esphome-ratgdo variant that I plan to use: https://github.com/ratgdo/esphome-ratgdo/tree/main/static, specifically this one:

https://github.com/ratgdo/esphome-ratgdo/blob/main/static/v25board_esp32_d1_mini.yaml

Kaldek, 2023-10-25:
> And 30$ for something like this, given the components and board design is a bit insane. Don’t you think?

No, the price is of no concern to me. I'm also developing a project based on an Arduino which I'll charge more than that.  I don't mind if I get copied but would hope to pay off the effort spent on the research and development.  The issue that got me started on this is the time to delivery of ratgdo and the shipping costs.

CrazyCoder, 2023-10-25:
> The issue that got me started on this is the time to delivery of ratgdo and the shipping costs.

Same here. I'd also need 2 boards for 2 garage doors and I already have all the components needed for DIY version. myQ stopped working with HA, so I need a working solution ASAP. Can't wait a month for the boards to be delivered.

Kaldek, 2023-10-25:
>  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

I have to ask again if you built one or have just created schematics.  The 10k resistor in series to the gate of AO3400A is off to me.  I've built similar circuits using Arduino and always use the 10k as a pulldown so there is no risk of a floating voltage tripping the MOSFET.  10k in series is usually for control of inrush current which I just don't see being an issue here.

tmeredyk, 2023-10-25:
im still just prototyping, i haven't breadboarded anything. im pretty sure its inverted in code but the gpio2 pin needs to be pulled high during boot or it will fail on the esp-12f. for the 10k maybe its not necessary. but thanks for the critique

Kaldek, 2023-10-25:
> im still just prototyping, i haven't breadboarded anything. im pretty sure its inverted in code but the gpio2 pin needs to be pulled high during boot or it will fail on the esp-12f. for the 10k maybe its not necessary. but thanks for the critique

No that's fine.  We should clarify then that my current schematic assumes use of a D1 mini rather than a raw ESP8266.

tmeredyk, 2023-10-25:
all good, i was just using the default pins on the ratdgo 2.0, if you'd like me to change them for the 2.5, it's no problem. its just i haven't seen the latest pcb. not sure what's changed. happy to add to this project

CrazyCoder, 2023-10-25:
Some findings. Dry contact GDO support is currently only in this branch of ratgdo: https://github.com/PaulWieland/ratgdo/tree/2.0-secplus1.0.

It's not available in the ratgdo-esphome yet. Related issue: https://github.com/ratgdo/esphome-ratgdo/issues/62.

My Genie obstruction sensors are ~12V. This post may be helpful regarding how they work: https://forum.allaboutcircuits.com/threads/genie-garage-door-sensors-used-elsewhere.59838/#post-402692:

> The way they work is the receiver adds a very narrow pulse train to the 12 V. line when it is detecting the emitter. The circuitry inside the door opener detects this signal.

Will verify it with the oscilloscope shortly.

Kaldek, 2023-10-26:
> all good, i was just using the default pins on the ratdgo 2.0, if you'd like me to change them for the 2.5, it's no problem. its just i haven't seen the latest pcb. not sure what's changed. happy to add to this project

The only change from a circuitry perspective was the change to D1 (GPIO5) for TX away from D4 (GPIO2).

CrazyCoder, 2023-10-26:
Genie obstruction detection pulse when not obstructed (HIGH when obstructed):

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

Voltage goes up to 12.5V (12.7V max). It looks like voltage divider will be needed to get it compatible with the current board version.

According to the code:

> // If at least 3 low pulses are counted within 50ms, the door is awake, not obstructed and we don't have to check anything else

There should be close to 20 low pulses in 50ms with Genie, so it might work.

rlowens, 2023-10-26:
Looking thru the issues in ratgdo I noticed a link to https://github.com/mariusmuja/esphome-ratgdo where the have this schematic:
https://github.com/mariusmuja/esphome-ratgdo/blob/main/static/gdo_schematic.png

So, that's a comparison if needed.

Not sure if @mariusmuja has any insight into how well his schematic is working?

mariusmuja, 2023-10-26:
> Not sure if @mariusmuja has any insight into how well his schematic is working?

As I mentioned on the original issue, this schematic is working fine for me (tested on 2 security+ 2.0 GDOs). I don't have a ratgdo board yet (one is on its way).
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
jgosnell56, 2023-11-06:
I am seeing an issue and wondered if anyone saw this or what could be causing my issue. When I use an external power source for my Ratgdo, everything works properly. When I pull the 3.3v source from the board following the diagram here (very bottom) [https://paulwieland.github.io/ratgdo/03_wiring_soldered.html](https://github.com/ratgdo/esphome-ratgdo/issues/url), my remotes drastically lose distance. They are pretty much useless unless I am standing inside the garage when pressing a button. I assume I am drawing too much power from the board causing the remote receiver to be underpowered. Is there another 3.3v source on the board I could solder to and try?

tmeredyk, 2023-11-06:
i haven't tried this but i would try and add ur own regulator off of the 12v rail

Kaldek, 2023-11-06:
> I am seeing an issue and wondered if anyone saw this or what could be causing my issue. When I use an external power source for my Ratgdo, everything works properly. When I pull the 3.3v source from the board following the diagram here (very bottom) [https://paulwieland.github.io/ratgdo/03_wiring_soldered.html](https://github.com/ratgdo/esphome-ratgdo/issues/url), my remotes drastically lose distance. They are pretty much useless unless I am standing inside the garage when pressing a button. I assume I am drawing too much power from the board causing the remote receiver to be underpowered. Is there another 3.3v source on the board I could solder to and try?

Yeah don't pull power from the garage door opener's board.  Either use an external supply or - if your GDO has it - the battery backup wires. These are 12v high power.  We have notes here in this repo on using a voltage regulator for this.

rlowens, 2023-11-12:
FYI: Paul has switched to an integrated ESP12F-based board for his new ratgdo v2.5i. It is "functionally the same as v2.5", but this is the first shot I've seen of the front of a v2.5+ board, if we want to try to understand what changed from v2.0.
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

rlowens, 2023-11-12:
I also found this shot of the ratgdo v2.5 without a D1 mini installed. I think I can confirm it has the same number of transistors and diodes as ratgdo v2.0 but 3 more resistors (2 more on the left and 1 more on the right):
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

My guess is that this is one more resistor for each of the AO3400A MOSFETs, probably a pull-down resistor as @Kaldek added, in addition to the series-resistor Paul already had on each of those.

foreverimagining, 2023-11-12:
If it helps any, I'm expecting my v2.5 to come in tomorrow (as long as USPS doesn't botch it again, since it's been in the area since 11/09). I was going to offer to provide any information/testing-I'm-capable-of you guys might be needing before I went ahead and installed it. I'm planning to make the second one I'll need for various reasons, and I'd likely rather base it off v2.5.

I can already tell you, from the picture of the v2.5i, that he's going to cheese off the 3D printing community again, though.

tmeredyk, 2023-11-12:
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

rlowens, 2023-11-12:
> offer to provide any information/testing-I'm-capable-of you guys might be needing before I went ahead and installed it. I'm planning to make the second one I'll need for various reasons, and I'd likely rather base it off v2.5.

That would be great. We'll need clear shots of the front and back without D1 mini installed, then probably some tracing with a continuity tester to confirm what connects to what.

foreverimagining, 2023-11-12:
> We'll need clear shots of the front and back without D1 mini installed, then probably some tracing with a continuity tester to confirm what connects to what.

I think I can manage that. Would you prefer I start a new issue with the pictures to make things a little more organized?

rlowens, 2023-11-12:
> Would you prefer I start a new issue with the pictures to make things a little more organized?

That sounds good.

Kaldek, 2023-11-12:
Re-opening for public discussion visibility.

Kaldek, 2023-11-12:
> FYI: Paul has switched to an integrated ESP12F-based board for his new ratgdo v2.5i. It is "functionally the same as v2.5", but this is the first shot I've seen of the front of a v2.5+ board, if we want to try to understand what changed from v2.0. 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

If Paul is building a complete unit including CH340 USB-to-serial and power regulation, it likely means expectation of sales volume and the reduced wholesale prices that come with that.

Kaldek, 2023-11-28:
Closing due to multiple pull requests which have updated all of our schematics based on information gathered from other issues.

Closed 2023-11-28.

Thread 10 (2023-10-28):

Wired and remote isn't turning on, what am I doing wrong?

mikekay1, 2023-10-28:
This is what I followed --
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

the black wire leads to R on the remote (confirmed)

in the next post is my wiring at GDO

mikekay1, 2023-10-28:
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

Kaldek, 2023-10-28:
Hi mate, it's possible you followed one of my busted-ass schematics which Fritzing keeps borking.  Check the v7 schematic and make sure your design follows that.  Most importantly make sure you don't have the red wire shorted to ground like I did in the v6 diagram.

If this was the problem I am really sorry.

mikekay1, 2023-10-28:
Hey Kal, thanks for the quick reply -- Ah shit I did follow v6 I thought that was the newest one. but still shouldn't remote work even with the esp32 off?

mikekay1, 2023-10-28:
for additional reference, I followed this from the supported boards readme:

https://github.com/Kaldek/rat-ratgdo/blob/main/ratgdo%20open%20source%20ESP-32_schem_v1.png

Kaldek, 2023-10-28:
> Hey Kal, thanks for the quick reply -- Ah shit I did follow v6 I thought that was the newest one. but still shouldn't remote work even with the esp32 off?

If the red wire is grounded the wall remote won't get any power, regardless of the ESP32.  Don't feel too bad about this BTW, when I was first reverse engineering this earlier in the week I grounded out the red wire like ten frickin' times.

Kaldek, 2023-10-28:
> for additional reference, I followed this from the supported boards readme:
>
> https://github.com/Kaldek/rat-ratgdo/blob/main/ratgdo%20open%20source%20ESP-32_schem_v1.png

I'm re-checking that diagram now and it looks correct. The other thing to be aware of is whether you may have the MOSFET pins flipped around.  Ignore the pin *numbering* on that diagram, it's Fritzing having the icons totally wrong.

Let me upload one with Source, Gate, and Drain labelled.

mikekay1, 2023-10-28:
but regardless, the remote should turn on even if the esp32 isn't on right? like doesn't this whole system work without anything turned on because it runs in parallel?

I had a buddy whos an electrical engineer check my work. Im pretty sure I am good with the mosfets, I got them back to back. Let me take a pic.

Kaldek, 2023-10-28:
Updated image:
https://github.com/Kaldek/rat-ratgdo/blob/main/images/ratgdo%20open%20source%20ESP-32_schem_v2.png

> but regardless, the remote should turn on even if the esp32 isn't on right? like doesn't this whole system work without anything turned on because it runs in parallel?

Not quite.  If the passive circuit design is wrong the whole Red wire is permanently grounded.

mikekay1, 2023-10-28:
Its impossible to take a picture of breadboard its so jam packed because I wanted to make aure I could fit it on a d1

Kaldek, 2023-10-28:
> Its impossible to take a picture of breadboard its so jam packed because I wanted to make aure I could fit it on a d1

Have a look at my D1 Mini breadboard that was my first working prototype and let me know if yours follows this?
https://github.com/Kaldek/rat-ratgdo/blob/main/Breadboard_working.png

mikekay1, 2023-10-28:
Yea followed it to a T, i assumed this green wire leads to the center pin...

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

Kaldek, 2023-10-28:
> Yea followed it to a T, i assumed this green wire leads to the center pin...

Yep, sure does.  The pins of the MOSFET are Source/Gate/Drain so the middle pin is Gate.

Check your MOSFET to make sure it's not shorted Gate to Ground.  It is the *classic* MOSFET failure mode.

mikekay1, 2023-10-28:
Hey bro, totally ripper, I looked at your schematic and actually lined up the ends pins on the n7000's back to back. what I outta do is short it to the center pin, because soo as I unplugged the chip it stopped pulling to ground and remote turned on. I think I need another drink haha!

Kaldek, 2023-10-28:
Also make sure with your ESP-32 setup that you check our updated notes.  We're pivoting back to using the v2.0 web installer option for anyone with an ESP-32 because the ESPHome flasher web page doesn't have the v2.5 ESP-32 settings available, and Paul Wieland hasn't even started offering the v2.5 settings on his downloader.

On an ESP-32, TX should therefore be connected to GPIO16!

mikekay1, 2023-10-28:
Yea I used 2.0, read that in the other thread, no need for 2.5 because I dont need dry contact support or additional(?) trip sensors... I will put a ultrasonic sensor attached to this esp32 for car detection as well...

mikekay1, 2023-10-28:
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

So yea, I actually followed that thread for pinouts but followed the schematics from v 2.0 is that not what I am supposed to be doing?

as for GPIO16, I went with 23,22 and 21 is that also not correct?

Kaldek, 2023-10-28:
> as for GPIO16, I went with 23,22 and 21 is that also not correct?

Yeah I'm sorry this is a bit confusing but it's IO16/GPIO16 rather than GPIO21.  I hadn't gotten around to updating the schematic.

mikekay1, 2023-10-28:
kk noted, I will update! and try again 👍

Kaldek, 2023-10-28:
> kk noted, I will update! and try again 👍

Give me 5 minutes to make sure I get it right.  I've got a rotten hangover.

Kaldek, 2023-10-28:
Righto I think I've fixed this up.
https://github.com/Kaldek/rat-ratgdo/blob/main/images/ratgdo%20open%20source%20ESP-32_schem_v3.png

mikekay1, 2023-10-28:
let me give it a whirl

mikekay1, 2023-10-28:
one quick question, if using 2n7000 x 2 configuration, are the gates in the same orientation as the schematic provided? I'm  waiting on the additional transistor from amazon.

Kaldek, 2023-10-28:
> one quick question, if using 2n7000 x 2 configuration, are the gates in the same orientation as the schematic provided? I'm waiting on the additional transistor from amazon.

They should be correct as per the schematic.  On the RX line, Gate is connected to the Red wire whereas on TX the Drain is connected to it.

mikekay1, 2023-10-28:
Yea sorry im a bit of a noob qhen it comes to bill of materials, i dont experience with these transitors.

Soon as i plih in my circuit the damn wall unit turns off aomething is wrong on my board and I cant pinpoint it

Kaldek, 2023-10-28:
> Yea sorry im a bit of a noob when it comes to bill of materials, i dont experience with these transitors.
>
> Soon as i plih in my circuit the damn wall unit turns off aomething is wrong on my board and I cant pinpoint it

Did you validate that neither of your MOSFETs have shorted Gate to Source?  Remove them from the board and do a continuity test.  That's step #1.  After that it's just that slow process of tracing each wire.  It's particularly tricky on breadboards.

Common issues I've had with my breadboard setups over the years:

- Accidentally connecting to the ground plane
- Not seeing that I've got two separate circuits connected to each other
- Getting parts installed backwards

sanjay900, 2023-10-28:
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

The amount of times i had MOSFETs with shorted Gate to Sources yesterday....

mikekay1, 2023-10-28:
Good tips here, ill try pulling the mosfets and tracing back.

Can someone give me an true to esp32 wiring diagram? Is that the auper updated one provided by @Kaldek?

poldim, 2023-10-28:
Can you guys confirm that schematics/ratgdo open source_schem_v7.png is accurate?  I can share the easyeda layout:

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

rlowens, 2023-10-28:
> Can you guys confirm that schematics/ratgdo open source_schem_v7.png is accurate?

Accurate to what? It does match your layout here. In ratgdo v2.0 the 10k resistor on the gate of IRLB8721 is in-series to D1 where we think it makes more sense to have it as a pull-down between gate and ground, as you have matched here.

> I think the matches the schematic just a bit cleaner.

Very nice, but I'd also like the Source/Gate/Drain labeled on the MOSFETs for those of us that aren't great at reading them.
Mine:
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

> Personally, I'd like to use D5/D6/D7 for the connections as they allow you to keep D1/D2 for hardware I2C.
That sounds fine to me. Just modify your device .yaml to use that.

rlowens, 2023-10-28:
> Good tips here, ill try pulling the mosfets and tracing back.
>
> Can someone give me an true to esp32 wiring diagram? Is that the auper updated one provided by @Kaldek?

https://github.com/Kaldek/rat-ratgdo/blob/main/schematics/ratgdo%20open%20source%20ESP-32_schem_v3.png  looks great

Kaldek, 2023-10-31:
> Can you guys confirm that schematics/ratgdo open source_schem_v7.png is accurate? I can share the easyeda layout
> I think the matches the schematic just a bit cleaner.

I like it mate, it's very clean and easy to read; easier than Ki-Cad even.  Can you do a pull request for creation of an easyeda folder with the files in it please.

mikekay1, 2023-10-31:
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

I also used this schematic but damn thing still aint working... Ill get back to it. If you are wanting for close this issue. It has more than enough revelent info in it.

Thanks for everyone's call to arms!

poldim, 2023-10-31:
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

I got a bit carried away  😛

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

I'll happily share but I want to build one of these things before I upload it.

Kaldek, 2023-10-31:
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

You know, I just **knew** someone who really liked laying out boards would come along.  This is quite the PCB.

Kaldek, 2023-10-31:
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

@mikekay1 do you want to try with 2n7000 if not already, or an RFP30N06LE?  Another guy just tried ten different IRLB8721 and none of them worked, which is...very weird.
https://github.com/Kaldek/rat-ratgdo/issues/5#issuecomment-1786406085

I am also very curious what your ESPHome console log is saying.  Is it seeing status updates (RX working) but can't send commands (TX not working), or getting lots of errors like "Collision detected"?

sanjay900, 2023-10-31:
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

I myself used two 2n7000s because they didn't have IRLB8721s in stock at my local electronics shop

mikekay1, 2023-11-01:
Im still trying to solve this, sorry guys thought I had it figured out! Thanks for all the comments, Ive double checked the circuit a million times and rebuilt countless times. My remote on the wall just shuts off. I have a model with batter backup do I need to bypass that for this to work? Are my grounds getting messed up? I wish I could send a picture of the board juat really hard to see anywl yall available on discord. This is driving me nuts!

I know I have the red wire correct, obstruction sensors connected. Even swapped to dual 2n7000 just to see if I could make it the same as Kaldeks protype board, might try and make it exactly! The same just for shits and giggles...

Closed 2023-10-31.

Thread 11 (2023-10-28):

Convert all schematics to Ki-Cad

Kaldek, 2023-10-28:
All schematics need to pivot from Fritzing to Ki-Cad as Fritzing is killing me with its routing bugs which I'm often not catching. 🤬

mikekay1, 2023-10-28:
Oh dude, totally just found a few errors in my breadboard:

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

these are a lifesaver -- but I'm still buying kaldek a brewski.. rage against the ratgdo, if I could buy one I would. just release the schematics dude :[

kudos to you man! doing great work here --

mikekay1, 2023-10-28:
to add, I'll help with drawing out some of the stuff soon as I get mine going...

bjhiltbrand, 2023-10-28:
I just started a PR with my stab at a KiCAD rendition.

https://github.com/Kaldek/rat-ratgdo/pull/13

Kaldek, 2023-10-29:
Accepted pull request to add the Ki-Cad files as they are in their own folder structure.  Time for me to open/review these in Ki-Cad, and then we can close this issue.

Kaldek, 2023-10-29:
@bjhiltbrand let's remove all of the power supply circuitry from the design; I was a bit cart-before-the-horse on this and it turns out there's not enough power available.  Other than that these look like we can use as the basic schematic for the repo.

bjhiltbrand, 2023-10-29:
Sounds good. I have removed those components, you want me to do another PR?

Kaldek, 2023-10-29:
> Sounds good. I have removed those components, you want me to do another PR?

Yep, hit it.

Kaldek, 2023-10-30:
@bjhiltbrand I'm going to learn how to use Ki-Cad shortly (promise!) but can you remove J2 from the schematic?   Unless it's there for other reasons of course.

bjhiltbrand, 2023-10-30:
@Kaldek, I put the 2 terminal blocks on there to give people options. In KiCAD, I usually design the schematic first, and then have the program put the component footprints from the schematic on the PCB view when developing a PCB. So, both of these terminal blocks link pins together, so that when someone builds this board, they can choose to use a terminal block with a 5mm pitch between pins (typical screw terminal), or a 2.5mm pitch (typical phoenix or dupont connector). I can remove one of the terminals from the schematic, but leave the footprint on the PCB design, if that would help clear things up?

Kaldek, 2023-10-31:
>  I can remove one of the terminals from the schematic, but leave the footprint on the PCB design, if that would help clear things up?

Yes it's probably worth doing that given there's already been some struggles with folks getting their prototypes up.  If needed we can work on basic vs. advanced schematics for the different audiences.   I honestly expected only the super technical folks to even consider trying this but I guess the backlog of ratgdo boards is making people desperate.

bjhiltbrand, 2023-10-31:
Alright. I removed the terminal block from the schematic, but not from the board design. I also changed the folder structure to have a self-contained kicad project for each variation on the board (D1 Mini - ESP32 vs. ESP8266). I have a couple more variations for bare ESP 8266 (12F) modules and ESP32 (WROOM) modules, but they're not ready to merge yet. I need to brush up one what pull-up/pull-down resistors I need and where they need to be placed first.

mikekay1, 2023-10-31:
Please shared the esp32 version when you have a chance!

bjhiltbrand, 2023-10-31:
> Please shared the esp32 version when you have a chance!

It's in PR right now. Once that's approved, it will be rolled in to the project. I think the pins are correct, but I'm not positive. I left the traces in place between the ESP8266 and ESP32 boards, so in theory, you should be able to use the same board for whichever D1Mini you choose. If the pin assignments need to be different, we will need to change that in the schematic.

Kaldek, 2023-11-01:
Closing as these now exist and can be improved/developed as needed.

Closed 2023-11-01.

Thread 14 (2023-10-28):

Using red wire for power.md

aasorokighb, 2023-10-28:
"The input capacitor of the voltage regulator module (usually rated 100uF) will be replaced with a 1000uF Low-ESR capacitor." Why would you put buffer cap on high voltage side? It is shorted by bus driver anyway (or is it protected by a diode?). Should you put it on 5V side and use 5v to 3.3v on board regulator for driving board? Sorry, I just ordered my stuff. It will take a few weeks till it arrives.

Kaldek, 2023-10-28:
It doesn't really matter now anyway as the voltage regulator and ESP can't be powered by the GDO's red wire.  I'm parking this for now.

Kaldek, 2023-10-28:
Issue closed as prototype of power supply using red wire current parked due to current draw too high.

CrazyCoder, 2023-10-28:
@Kaldek Do you think it may work for Genie using the obstruction sensor wire that has ~12V?

Kaldek, 2023-10-28:
> @Kaldek Do you think it may work for Genie using the obstruction sensor wire that has ~12V?

If you can find a voltage source that can take the current, absolutely.

CrazyCoder, 2023-10-28:
I mean the existing sensors that are already installed and wired. They have 12V on them, but I'm not sure what extra current their power source can provide. I'm afraid to damage the Genie by trying to pull too much current for ESP32 via the buck converter.

CrazyCoder, 2023-10-28:
I gave it a try and it didn't work. Even 0.3A current is too much for the obstruction sensor, and its light goes off when I plug my test board.

The worst part is that even a voltage divider needed to read the pulses from the sensor with ESP32 seems to affect the sensor (its indicator LED becomes dimmer).

Maybe an optocoupler will work better?

Kaldek, 2023-10-28:
> I gave it a try and it didn't work. Even 0.3A current is too much for the obstruction sensor, and its light goes off when I plug my test board.

Yeah it's a bit of a bummer, but I suppose there's no real issue with using external power via USB.  It's mainly going to be an issue for development of a raw board using an ESP-12F for example.  Arguably any design which removes the USB interface is a bit of a pain though because reflashing the chip becomes annoying unless the reflash can be done OTA (which it generally can), and the initial flash before building using an ESP flashing cradle is also more work than just connecting a D1 Mini board to USB.

rlowens, 2023-10-29:
I plan on opening up my GDO and tapping 3.3v from the board.

alexyao2015, 2024-09-15:
Has anyone tried putting a large capacitor on the input to see if smoothing the power consumption allows the esp to be powered?

Kaldek, 2024-09-16:
> Has anyone tried putting a large capacitor on the input to see if smoothing the power consumption allows the esp to be powered?

It's just too much current.  A capacitor won't help unfortunately.

alexyao2015, 2024-09-16:
That's really surprising considering we are stepping down from 12v. How is it using that much current?

Kaldek, 2024-09-16:
The ESP8266 pulls between 0.11 and 0.2 amps of current.  I suspect the WiFi is what pulls the most, but the point is basically moot; as soon as the ESP8266 tries to power up the voltage collapses.  The ESP8266 won't boot and the wall controller shuts off.

Closed 2023-10-28.

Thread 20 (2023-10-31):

Gerber files do not match KiCad files

dpeart, 2023-10-31:
When I look at the provided Gerber files they are not the same as the KiCad files.

The Gerber files have a large capacitor and only have a two pin terminals.

Gerber
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

KiCad
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

Kaldek, 2023-10-31:
@bjhiltbrand do we need another pull request?

bjhiltbrand, 2023-10-31:
Weird. I am regenerating the gerber files as I make changes. Let me look to see why they don't appear to be updating.

bjhiltbrand, 2023-10-31:
I would assume that the old files didn't get cleared out through the renaming of the project that I did recently, so both sets of gerber files existed for the older project name and the new project. The older files were then the ones chosen in a gerber viewer. I forcibly deleted the old gerber files and recreated the gerber file set. I have submitted a new PR.

Kaldek, 2023-10-31:
@bjhiltbrand no stress here mate.  It is the problem we all face once we submit work to the world.  If you'd prefer not to get too involved just let me know.

bjhiltbrand, 2023-10-31:
I'm good, no worries. :)

dpeart, 2023-11-01:
I put an order in for 10 boards.  Built and assembled they are $3.5 each, add a$2.5 for the D1 Mini and I'm done.  All I have to do is solder in the D1 Mini.

Thanks

bjhiltbrand, 2023-11-01:
>  I put an order in for 10 boards.  Built and assembled they are $3.5 each, add a$2.5 for the D1 Mini and I'm done.  All I have to do is solder in the D1 Mini.
>
> Thanks

Here's hoping they work. I haven't had a chance to order mine yet. :)

pleasanthill17, 2023-11-04:
> I put an order in for 10 boards. Built and assembled they are $3.5 each, add a$2.5 for the D1 Mini and I'm done. All I have to do is solder in the D1 Mini.
>
> Thanks

I am struggling with Kicad to gerber conversion. Is there anyway you write a few lines what you did with the files to get the gerber files ordered or share your files/project on oshw. Also where did you get it assembled for $3.5.

Thanks !

dpeart, 2023-11-04:
In KiCad you use file->fabrication outputs.  Output each file option.  Then zip up the directory you saved them in.

I use JLCPCB to make my boards. I've used them before and they are great.

On JLPCB you upload the zip file and it will extract everything about the board.  You can then just order the boards, but I also chose to have them assembled.  There you select that option, and you have to upload the Bill Of Materials and placement files.  This is where I had to make changes.  They give you an example of each, so it is easy to create the file formats they need based on the files KiCad export.

Then verify placement and make your order.  I had to manually move the screw terminal as KiCad calculated the placement incorrectly but it is easy to do on their website.  Everyone gets a $10 of coupon so use that.

dolfelt, 2023-11-09:
@dpeart How did you find the correct terminals in JLC? It doesn't find them from the CPL and when I search none of them are showing up for the 3 terminals. Thoughts?

dpeart, 2023-11-09:
Here is the BOM I used:
`Comment	Designator	Footprint
10k	R1,R2,R3	R_0805_2012Metric
WeMos_D1_mini	U1	WEMOS_D1_mini_light
AO3400A	Q2	SOT-23 AO3400A
2n7002	Q1	SOT-23 2n7002
Screw_Terminal_01x03	J1	TerminalBlock_Phoenix_MDKS-`

bjhiltbrand, 2023-11-09:
Also, you only need to choose 1 option out of the 3 on the board to have populated, if you want. You can also choose any terminal you want with a 5mm, 3.5mm, or 2.54mm pitch. I put them all there to allow options for the various pitches. Here are the different types of connectors I had in mind:

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

dolfelt, 2023-11-09:
Thanks for the help! Do the terminals get in the way of the USB that powers the ESP32?

Anyone have an example of a fully assembled PCB?

bjhiltbrand, 2023-11-10:
Ha! I never really thought about it. I just measured 4 USB cables (1 USB-C and 3 Micro USB), and 3 of them were about 18-20mm, with one being ~21mm. The kicad design measures 20mm between the D1 mini and J1. Also, if your USB is on top of your D1 mini, I measure it at 11mm off the board (assuming you are using sockets soldered to the rat-ratgdo and pins soldered to the D1 mini. The blue terminal pictured above (this is the 5mm pitch terminal that would fit in J1) is the one that might have clearance issues from the USB. It measures 10mm off the board. So, it might be a bit tight, but should fit fine.

I don't think anyone has an example yet, as we're all waiting for the slow boat from China right now. :)

bjhiltbrand, 2023-11-10:
While not the same project, this is the board that informed much of my design, and where I have extra parts for building mine when my boards get here. The D1 mini is designed to float over the top of the terminals, as long as the USB port is on the top of the D1 mini (I have seen some that have the port on the bottom).

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

dolfelt, 2023-11-10:
@bjhiltbrand or @dpeart, any idea how to get pin sockets added by JLC/PCBWay? I've tried adding a new footprint in kicad, but that feels like the wrong approach since it updates the pads. If it's not possible I can just solder them myself, but trying to save some time since it's only a few cents more for more parts added.

I've also updated the design to guarantee no conflicts with the USB by rotating the board sideways. Would also allow additional terminals on the other side if it's ever necessary.
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

bjhiltbrand, 2023-11-10:
I'm not sure on how best to only have the sockets populated by a board house. I've never had one build a board for me before, as I prefer to do the soldering myself. I wonder if you can just put that in notes somewhere, that you would like to use 4- 1x10 sockets on the board? I like the redesign. You should commit that as another option in the kicad files folder. I noticed on my design just barely, that the footprint for the ESP32 didn't actually keep out the copper on the ground plane for the antenna. I have fixed that and submitted a new PR for it. Please check your redesign for the same issue before making your board.

dolfelt, 2023-11-10:
Whoops! Definitely already submitted it for build.

bjhiltbrand, 2023-11-10:
I don't know that it will make a difference, now that I think about it. If you have the D1 mini installed using sockets and pins, it will be above the board, and separated enough to have a negligible effect on wifi signal anyway.

dpeart, 2023-11-10:
You have to put the pins into the schematic and set their footprint.  You can always solder them on when you get the board back.  this what I'm going to do.  They came with my D1 mini.

dolfelt, 2023-11-10:
Thanks for all your help! Now I wait for the board and work on HomeKit integration. Doing this all because of the blocked MyQ API. And local is better anyways.

bjhiltbrand, 2023-11-10:
> Thanks for all your help! Now I wait for the board and work on HomeKit integration. Doing this all because of the blocked MyQ API. And local is better anyways.

So, I'm building at least 3 of these - 2 for me and 1 for my dad. I use Home Assistant, so that should be pretty straightforward to integrate. My dad, however, uses HomeKit/HomeBridge. I have been having trouble figuring out if there is an integration ready yet for HomeBridge. What route are you planning on going to integrate yours with HomeKit?

dpeart, 2023-11-10:
I should get my 10 boards on the 22nd.  I have 6 to install and my brother 4.  Hopefully they work well :)
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
dolfelt, 2023-11-17:
@Kaldek @bjhiltbrand Got my PCBs from China yesterday. Exciting!

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

Got it all hooked up, only to realize that my jackshaft opener (RJO20) falls into the Security+ 1.0 category and nothing is working. Guess I wait and see if the Sec+ 1.0 update to the ESPHome fork will work.

Do we know if this board with work with 1.0? Does it match the v2.5 specs like it says in the Readme or just the 2.0 board? Excited to test it out once something is released.

dpeart, 2023-11-17:
Got my boards today as well.

bjhiltbrand, 2023-11-17:
Nice! My components should be here today and my boards should be here tomorrow. I can't wait!

bjhiltbrand, 2023-11-17:
> Also, @bjhiltbrand I'm pretty sure the Black and White labels for the terminals are reversed. 😬

Oh S***. I had that fixed at one point! I must have had it revert. Sorry about that. It looks like it's still good on the D1 mini 8266 version, but the other designs all have them switched. I'll fix that right now.

bjhiltbrand, 2023-11-17:
> Does it match the v2.5 specs like it says in the Readme or just the 2.0 board?

It should match the 2.5 specs.

bjhiltbrand, 2023-11-17:
@dolfelt, can you double check pin D7 on your ESP32-wide board? it should have continuity, but when I was fixing the silkscreen issues, I ran it through design rules checker and there were a bunch of errors. Once of which was that KiCAD didn't show a trace to follow from the schematic to the board. I updated the board from the schematic, and KiCAD brought in a new ESP32 footprint. I deleted and re-created the trace from the terminal, through the resistors, and to the pin, and I don't think it made a difference in the board you had made, but I figured I would let you know. Where I didn't design that variant, I figured I'd ask you for verification, since you did. ;)

dpeart, 2023-11-17:
Mine is with the D1 Mini

rlowens, 2023-11-17:
> > Does it match the v2.5 specs like it says in the Readme or just the 2.0 board?
>
> It should match the 2.5 specs.

It matches the gpio pins used by the ratgdo v2.5, but the v2.5 does have a few more resistors which we just found out about. https://github.com/Kaldek/rat-ratgdo/issues/44

dolfelt, 2023-11-17:
@rlowens I guess it's back to prototyping! 😄

dolfelt, 2023-11-17:
> @dolfelt, can you double check pin D7 on your ESP32-wide board? it should have continuity, but when I was fixing the silkscreen issues, I ran it through design rules checker and there were a bunch of errors. Once of which was that KiCAD didn't show a trace to follow from the schematic to the board. I updated the board from the schematic, and KiCAD brought in a new ESP32 footprint. I deleted and re-created the trace from the terminal, through the resistors, and to the pin, and I don't think it made a difference in the board you had made, but I figured I would let you know. Where I didn't design that variant, I figured I'd ask you for verification, since you did. ;)
>
> Also, I gotta say... that GitHub action to build the gerbers is slick!

I’ll take a look. Do you know if there’s a way to do multiple boards with a single schematics? Probably worth trying to keep a single schematic per board vs multiple.

bjhiltbrand, 2023-11-17:
I don't know. I'm not overly well-versed in KiCAD. I googled that question before (since the board layout would be the same for all D1 mini (ESP32 and 8266) modules, but I didn't spend a lot of time on searching and didn't find anything real quick.

dolfelt, 2023-11-18:
I’m not either @bjhiltbrand. Software engineer by trade, but just barely an electronics tinkerer. 😅

bjhiltbrand, 2023-11-18:
> I’m not either @bjhiltbrand. Software engineer by trade, but just barely an electronics tinkerer. 😅

Haha. Same here. QC/DevOps Engineer by trade, but really like the whole open hardware concept.

bjhiltbrand, 2023-11-21:
Got my boards and built it today. Works great powered off the battery backup.
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

Kaldek, 2023-11-21:
> I’m not either @bjhiltbrand. Software engineer by trade, but just barely an electronics tinkerer. 😅

Same same.  Well, InfoSec architect but same on the tinkerer level.

dpeart, 2023-11-21:
That is a clean looking board.

Closed 2023-10-31.

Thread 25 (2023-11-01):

IRLB8721 is **NOT** suitable

Kaldek, 2023-11-01:
We have discovered that the IRLB8721 does not switch at all due to it [needing current from Drain to Source for switching](https://forums.adafruit.com/viewtopic.php?p=446184).

All schematics must be updated to use either the 2n7000 or the RFP30N06LE.

For the attention of all who have submitted content:
@bjhiltbrand
@poldim
@rlowens

For the attention of known people with issues:
@rohinrohin
@vaidehi-joshi
@sanjay900
@ccutrer

Massive apologies to all who have been bitten by this problem.

sanjay900, 2023-11-01:
Thankfully i wasn't even able to get my hands on the `IRLB8721` so im already using a `2n7000`

bjhiltbrand, 2023-11-02:
So far, for the KiCAD schematics, I opted for SMD components, so I was using AO3400A mosfets instead of IRLB8721 mosfets. You think the schematics are still good with the AO3400A mosfets? I would assume we are still good, as the On-Resistance vs. Gate Voltage mentioned in the link you posted shows the mosfet not responding until it hits 4-5v, whereas the same graph for the AO3400A shows it responding at 2-3v.

ccutrer, 2023-11-02:
Switching from IRLB8721 to another 2n7000 fixed it. I now have full control. What would the difference be with a RFP30N06LE (I have two more to build)?

knissdesign, 2023-11-02:
I just built this project today, with the now-unsuitable IRLB8721. Can you define what symptoms arise from this? I’ve got the project successfully running but it seems most times I have to send commands twice for the garage door to respond, sometimes with delay. Curious if this IRLB8721 could be my issue? Logs in the web interface specify:

[component:214] | Component preferences took a long time for an operation (0.06 s).
[component:215] | Components should block for at most 20-30ms.

Thank you!

ccutrer, 2023-11-02:
My symptom was I had complete status, but no commands would ever work.

Kaldek, 2023-11-02:
> Switching from IRLB8721 to another 2n7000 fixed it. I now have full control. What would the difference be with a RFP30N06LE (I have two more to build)?

2n7000 requires 3v to fully switch on whereas the RFPO30N06LE only needs 2 volts.  GPIO voltage is 3.3v which is borderline if there is any voltage sag.  So, reliable data transmissions might be an issue using 2n7000.

Kaldek, 2023-11-02:
> I just built this project today, with the now-unsuitable IRLB8721. Can you define what symptoms arise from this? I’ve got the project successfully running but it seems most times I have to send commands twice for the garage door to respond, sometimes with delay. Curious if this IRLB8721 could be my issue?

Yes, it could.  The issue with the IRLB8721 will be that it either does not switch the signal at all or will do it unreliably.  I don't know if your log entries are related but you could check the C++ code for those errors to see what the triggering conditions are.

Kaldek, 2023-11-02:
> So far, for the KiCAD schematics, I opted for SMD components, so I was using AO3400A mosfets instead of IRLB8721 mosfets. You think the schematics are still good with the AO3400A mosfets? I would assume we are still good, as the On-Resistance vs. Gate Voltage mentioned in the link you posted shows the mosfet not responding until it hits 4-5v, whereas the same graph for the AO3400A shows it responding at 2-3v.

They will be fine if you use the AO3400A as that's what the original design from Paul Wieland uses.

CrazyCoder, 2023-11-02:
RFP30n06le is considered obsolete. Maybe find a better replacement option?

Kaldek, 2023-11-02:
> RFP30n06le is considered obsolete. Maybe find a better replacement option?

Hmm, maybe we just stick with the 2n7000?  I've had zero issues with mine.

sanjay900, 2023-11-02:
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

I get that log as well, i don't actually think it's a real problem, i've seen it on a bunch of ESPhome projects

brettcp, 2023-11-02:
Thank you for this!  I'm fairly new to following schematics but I was fairly confident I had everything right.  I could see the correct status of everything, but I wasn't able to get any response when sending commands.  After swapping the IRLB8721 for a 2N7000, commands are now working as expected.

Ordered some RFP30N06LE already and will move this from a breadboard over to a proper ESP8266 shield.

sanjay900, 2023-11-02:
> > RFP30n06le is considered obsolete. Maybe find a better replacement option?
>
> Hmm, maybe we just stick with the 2n7000? I've had zero issues with mine.

I also second this, i have no issues with mine either.

knissdesign, 2023-11-02:
> > I just built this project today, with the now-unsuitable IRLB8721. Can you define what symptoms arise from this? I’ve got the project successfully running but it seems most times I have to send commands twice for the garage door to respond, sometimes with delay. Curious if this IRLB8721 could be my issue?
>
> Yes, it could. The issue with the IRLB8721 will be that it either does not switch the signal at all or will do it unreliably. I don't know if your log entries are related but you could check the C++ code for those errors to see what the triggering conditions are.

Update for anyone else troubleshooting! I replaced the IRLB8721 with a 2n7000 and everything is now working as expected. The IRLB was indeed the cause for my symptoms.

The 2n7000 currently seems to be successful, to tag on to others saying the same.

Kaldek, 2023-11-02:
Well folks, what do we think?  @rlowens shall we just recommend a 2n7000 for through-hole and be done with it?  I haven't had a single issue.

sanjay900, 2023-11-02:
Has anybody here had a problem with the 2n7000?

CrazyCoder, 2023-11-02:
> Has anybody here had a problem with the 2n7000?

I'm not sure how well it will work for the dry contact mode with no security. In my testing, it was not dropping voltage to zero like RFP30N06LE did: https://github.com/Kaldek/rat-ratgdo/issues/5#issuecomment-1786383189.

Switching serial line is one thing, but maybe it will have issues with an old-school control panel and LED when it needs to properly short it to the ground?

I didn't test it on the real device, so it might work just fine.

rlowens, 2023-11-02:
I think we should list several tested and possible parts and what problems they have/might have.

Browsing around digikey for MOSFETS similar to AO3400A (which the ratgdo v2.0 uses) found this:
[FDU6512A](https://www.digikey.com/en/products/detail/rochester-electronics-llc/FDU6512A/11536494) (obsolete but in stock, $0.78/each)
[IRLU3802PBF](https://www.digikey.com/en/products/detail/international-rectifier/IRLU3802PBF/12616676) (active status, $0.48/each)
or [these search results](https://www.digikey.com/en/products/filter/single-fets-mosfets/278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)
Do any of those look good? I'm not an expert here.

Kaldek, 2023-11-02:
> I think we should list several tested and possible parts and what problems they have/might have.
> Do any of those look good? I'm not an expert here.

Yeah unfortunately neither am I and that's how I got into the IRLB8721 mess.
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
Kaldek, 2023-11-08:
> https://www.mouser.com/datasheet/2/196/Infineon_IRLB8743_DataSheet_v01_01_EN-3363390.pdf specs look better then the IRLB8721. I don't plan on switching mine out, so does someone else want to try this one?

That's worse!  It's input capacitance is 5 times that of the IRLB8721 and that's what we believe is causing the IRLB8721 to not switch when driven by the ESP8266.

ccutrer, 2023-11-08:
Oh well, like I said, I only barely know what I'm talking about. I was looking at the R(DS) vs. V graph of both. The 8721 resistance doesn't drop significantly until nearly 5V.

Kaldek, 2023-11-08:
The issue here is that the most suitable MOSFETs are the AO3400A as used in the original ratgdo PCB or a BSS138 (very similar).  Both are SMD, not through-hole.

For TO-92 it's really limited and so far it looks like the 2n7000 but it might depend on the batch you get as to how happily it switches at 3.3 volts.

CrazyCoder, 2023-11-08:
One option for through-hole/breadboard design would be to get the original AO3400A and a [SOT23-3 to DIP adapter](https://www.amazon.com/Chironal-Double-Side-SOT23-3-Adapter-Converter/dp/B07MQBF2DD/).

Kaldek, 2023-11-08:
> One option for through-hole/breadboard design would be to get the original AO3400A and a [SOT23-3 to DIP adapter](https://www.amazon.com/Chironal-Double-Side-SOT23-3-Adapter-Converter/dp/B07MQBF2DD/).

Bugger me, if it's that easy we should just recommend this.

jsb5151, 2023-11-09:
Welp I just got my shipment of RFP30N06LE!  However, I’m wondering if that model can be used for both MOSFETs?  I don’t have any 2N7000s handy.

Kaldek, 2023-11-09:
> Welp I just got my shipment of RFP30N06LE! However, I’m wondering if that model can be used for both MOSFETs? I don’t have any 2N7000s handy.

Can't hurt to try; on RX you're using a 12v trigger to drive the MOSFET on/off and therefore pull 3.3v low or not on the RX pin of the ESP.  If you can see data on the bus, it's working fine.

rlowens, 2023-11-09:
> Can't hurt to try;

Well, can't it? The "Absolute Maximum Rating, Gate to Source Voltage" is +10V for[ the RFP30N06LE ](https://www.mouser.com/datasheet/2/308/rfp30n06le-1195941.pdf) so I think it might not survive 12V.

Kaldek, 2023-11-09:
> > Can't hurt to try;
>
> Well, can't it? The "Absolute Maximum Rating, Gate to Source Voltage" is +10V for[ the RFP30N06LE ](https://www.mouser.com/datasheet/2/308/rfp30n06le-1195941.pdf) so I think it might not survive 12V.

Ah I missed that.  Too many stats, too little time.  😬

jshatch, 2023-11-09:
> > I can confirm that RFP30N06LE works. And more reliably than my door with a 2N7000. The latter I often have to send commands twice, but with the former it works first time every time.
>
> Way to complicate my life as I was just about to commit to saying "use a 2n7000" 🤣

Mine using 2x 2N7000's seems to work the first time every time, haven't had to resend any commands.

Kaldek, 2023-11-09:
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

Yeah same here.  We're going to pivot to recommending the AO3400A mounted to a SOT23 to DIP converter board.  It just simplifies everything as the "recommended option".   Even though the 2n7000 works for many.

bdistin, 2023-11-10:
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

Just built my first one tonight. Worked first time every time with 2x 2N7000s. Didn't know about this issue, but noticed the pics showed 2x 2N7000s, and yoloed it even though I also bought the other transistor.
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

Kaldek, 2023-11-10:
Yeah it's weird.  My ESP8266 is putting out 3.2 volts and seems to switch the 2n7000 reliably.

sanjay900, 2023-11-10:
> Yeah it's weird. My ESP8266 is putting out 3.2 volts and seems to switch the 2n7000 reliably.

Mine is also reliable

jshatch, 2023-11-10:
Well I built my second one and used a RFP30N06LE this time, works about the same except for I get errors on that one that say:
```
00:24:21 | [W] | [component:214] | Component preferences took a long time for an operation (0.07 s).
00:24:21 | [W] | [component:215] | Components should block for at most 20-30ms.
```
I suppressed the errors because otherwise it works perfectly but I wonder if it has something to do with that MOSFET.  Maybe it's a little slower?

ccutrer, 2023-11-10:
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

I saw that with my first one I built with a 2n7000, but not the RFP30N06LE ones. Go figure. But yeah, I wouldn't worry about it.

jshatch, 2023-11-10:
It's probably internal differences between the two openers I have then. I would check by swapping the ratgdo's but I don't want to... 😁

Kaldek, 2023-11-12:
Recommending sn7000 for through-hole and closing this issue.  SMD recommendations will stick with what Paul Wieland uses.

tronikos, 2023-11-16:
FAQ.md still mentions IRLB8721

Closed 2023-11-12.

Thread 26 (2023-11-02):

Support for security +1.0 GDO

vaidehi-joshi, 2023-11-02:
Following up on this in a new issue since we are using the D1 Mini now.

To summarize,
1. We are using the D1Mini ESP8266MOD
2. We have a security 1+ GDO (purple learn button)
3. We are using 2x 2n7000n Transistors
4. Obstruction sensor is working
5. We used native ratgdo and flashed `ratgdo v2.26, Security + 2.0 (secplus 1.0 alpha)`
6. Logs show `Wall panel detected` and when I try to open the door, it says `Door is not moving`

Any help greatly appreciated!
😞

sanjay900, 2023-11-02:
Are there any more logs than that?
I presume this is after setting the control protocol to security 1+ correct?

Kaldek, 2023-11-02:
Unfortunately I haven't looked into what the code tries to do for these types of openers.  What I recommend is done is a review of the C++ code for these openers to see what the TX GPIO tries to do when a door toggle is pressed.    Once it's clear what the code is trying to do, I would use a two-channel oscilloscope monitoring the GPIO pin (MOSFET gate pin), and the drain of the MOSFET (red wire).

The GPIO pin should be LOW unless commanded, and the drain of the MOSFET should be HIGH unless commanded.

sanjay900, 2023-11-02:
Reading the code it does seem like it is just using it as a serial line, much like security+ 2.0

Kaldek, 2023-11-02:
> Reading the code it does seem like it is just using it as a serial line, much like security+ 2.0

Hmmm, in that case I would definitely bust out the oscilloscope.

sanjay900, 2023-11-02:
One thing i did note is that it is at a lower baud rate.
@vaidehi-joshi Does the door move if you try to open and close it from mqtt?
and do you get updates if you open the door via other means, or is both receiving and transmitting broken?

Kaldek, 2023-11-02:
> One thing i did note is that it is at a lower baud rate.

Just in case anyone is concerned by that, a lower baud rate would - if anything - be helpful as the switching speeds of the MOSFET are lower.  As speeds increase, switch timing becomes important, and then critical.  For lower baud rates, there's more "wiggle room".

rohinrohin, 2023-11-03:
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

door doesn't move if we try to open/close from MQTT. The only thing that works is the obstruction sensor.

Is there any other combination of ESPs (32/8266/..) has been tested for a Security 1+ device?

Kaldek, 2023-11-04:
> And @Kaldek - we unfortunately do not have an oscilloscope. Could buy one if you have a good affordable recommendation.

Hantek 2D72 - cheap, portable, dual channel and is also a multimeter.

sanjay900, 2023-11-04:
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

Also what wiring schematic did you follow?

tronikos, 2023-11-07:
Does it work in emulation mode without the wall panel? You will see in the logs "No wall panel detected. Switching to emulation mode."

Which wall panel do you have? Apparently it doesn't work with 78LM and maybe others and this is the reason there is no ESPHome port yet for security+ 1.0. See https://github.com/ratgdo/esphome-ratgdo/issues/70 and https://github.com/PaulWieland/ratgdo/issues/101.

Can you rename the issue? The use of D1 mini has nothing to do with this issue. It's the security+ 1.0 that is not supported well yet.

I also have security+ 1.0 and I'm waiting for this to be resolved before I order the transistors just in case we need different ones to make it work.

tronikos, 2023-11-08:
What's the reason you used v2.26 which is meant for v2 boards instead of the latest v2.51 which is meant for v2.5 boards? The schematics in this repo are based on v2.5. The TX pin changed between the 2 board revisions (from D4 to D1). So make sure you use the correct firmware and the correct pins.

Kaldek, 2023-11-09:
> What's the reason you used v2.26 which is meant for v2 boards instead of the latest v2.51 which is meant for v2.5 boards? The schematics in this repo are based on v2.5. The TX pin changed between the 2 board revisions (from D4 to D1). So make sure you use the correct firmware and the correct pins.

2.51 wasn't available last week.  It must have been added in the last day or so!

rohinrohin, 2023-11-09:
Will do a quick test with this firmware today. Thanks!

Just to clarify, I shall use the exact same pin out as in the schematic here and flash the latest firmware right?

rohinrohin, 2023-11-09:
> Is there a 2.51 ESPhome firmware? the lastest I can flash is 2.50 which lacks the option to set it into security 1 mode.

No I think ESPHome still doesn't support Security 1+, this is native ratgdo.

pizzaboy192, 2023-11-09:
> No I think ESPHome still doesn't support Security 1+, this is native ratgdo.

Thanks! I have my ratratgdo running the 2.51 Security+1.0 firmware, on power up it will trigger a door open or close event but then fail to respond. It was cold and last last night when I wired it up so I'll investigate today or tonight what I may have done wrong.

rlowens, 2023-11-09:
> Is there a 2.51 ESPhome firmware?

Technically, the ESPhome firmware is really just versioned by the date of compilation. The latest update on the esphome-ratgdo firmware was 16 hours ago (adding a timeout for Security+ 2.0 motion detectors so they can trigger more often than the light turning off). https://github.com/ratgdo/esphome-ratgdo

> the lastest I can flash is 2.50 which lacks the option to set it into security 1 mode.

No, the "2.50" you are referring to here is ratgdo HARDWARE version 2.5, not firmware version. There is no version number for the esphome-ratgdo firmware as far as I can tell, just compile date.

> No I think ESPHome still doesn't support Security 1+, this is native ratgdo.

You are correct that esphome-ratgdo doesn't support Sercurity+ 1.0 yet (they are still ironing out the Security+ 1.0 support before adding it). And since it was split out as a separate project the correct name is "mqtt-ratgdo" https://github.com/ratgdo/mqtt-ratgdo

There is also the (in-process) https://github.com/ratgdo/homekit-ratgdo firmware.

pizzaboy192, 2023-11-13:
Turns out, just like there's some weird combinations of "Security 2.0" openers where the door pads are controlled by 1.0, my "Security +" opener uses Security+ for RF communication, but accepts dry contact input on the opener itself. Good job Liftmaster.

sanjay900, 2023-11-13:
> Turns out, just like there's some weird combinations of "Security 2.0" openers where the door pads are controlled by 1.0, my "Security +" opener uses Security+ for RF communication, but accepts dry contact input on the opener itself. Good job Liftmaster.

There are security 2+ openers that have a serial line and a dry contact line, the serial line you connect ratgdo to ends up being green on those units, and the dry contact line is just that, it's simply just dry contact

Kaldek, 2023-11-28:
@vaidehi-joshi any updates on your progress here?

godmar, 2023-11-28:
I too have a purple learning button and (I believe) an LM78 wall button. I was going to wire up rat-ratgdo and try this, but what I read in these threads concerns me a little bit (though time permitting over the holidays, perhaps I'll try to help. And I do have an oscilloscope I could put to use ;-)).

My questions include:

- what is emulation mode?
- what is the significance of the wall terminal?  Does ratgdo somehow need to sniff traffic between the opener and panel? I will say that I won't start the project if there's a risk of losing the ability to open the garage door with the wall panel.
- how do "dumb" panel like the LM78 actually work?  They seem to be able to reliably switch the garage door from what I can see. (and related, why don't we just tap into them and side-step the whole security protocol)
- what is the significance of the choice of MOSFET?  There seem to be two different schematics, some with 2n7000n and some where one of the transistors is replaced by a AO3400A, and I think I found one post where an entirely different type was discussed.
- even in Wieland's version of hardware+software support for 1.0 seems to be partial (not supported for ESPhome, partially supported for the [MQTT version](https://paulwieland.github.io/ratgdo/01_features.html)). The way I understand it, MQTT is the messaging protocol from the MCU to a server, whereas the difficulties with the Security+ 1.0 protocol results from understanding the signal level protocol, which should be the same for the ESP Home/Home Assistant version. Perhaps it's just a matter of porting it.

sanjay900, 2023-11-28:
Yeah, he plans on porting it once the support is fully working for the mqtt version, since there are still a few cases where it isn't working yet

Kaldek, 2023-11-28:
> My questions include:

Most of these questions are valid for Paul Wieland but not this repo.  The only question I can provide any response to is about the choice of MOSFET, and it relies on the historical context of this repo.

We had no boards to test with, only images.  Paul Wieland refuses to provide the schematic, so we had to reverse engineer what we could.  We worked out after a couple of days that the part marked "XOYL" is an AO3400A MOSFET.  I personally had no access to any N-channel MOSFETs other than some 2n7000 units (since they are so common).  I tried it, and it worked, so I had some basic Fritzing-based diagrams using the 2n7000.

And that's when the community entered the fray, which caused us to constantly update and change recommendations, and then change them back again after debate, or discovery that the recommendations don't work at all.  It leads to lag in the documentation, or sometimes I forget that there is a reference to the older recommended part.  It's made worse by the fact that some of the folks who come here just want to knock up a home made through-hole prototype and be done with it, whereas other folks are keen to generate schematics and gerber files for SMD based board designs.

Kaldek, 2023-12-26:
Closing due to issue not related to this repo, and lack of updates.

Closed 2023-12-26.

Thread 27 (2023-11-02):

Finally got a working board following breadboard prototype

mikekay1, 2023-11-02:
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

The remote is now working while plugged in but need help with yaml and gpio mapping? Do I need to put this into the yaml or should this work out the box with esphome v2.0 software?

Thank guys!

mikekay1, 2023-11-02:
Some more info on this, im so close I can taste it.

When tx and rx are correct per schematic I get collision detected which floods the logs... See first three pictures.

When I reverse the TX and RX problem goes away but no status is given and nothing works.

Last picture shows my wiring to GDO

Any help would be appreciated!

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

Kaldek, 2023-11-02:
Flash v2.5 and then do the YAML edit is what I would recommend.

If you can't work out to upload a fully custom YAML to the board, I would use the default pins for now, which means just using this YAML file: from https://github.com/ratgdo/esphome-ratgdo/blob/main/static/v25board_esp32_d1_mini.yaml

Choosing which YAML file to use means you have to have ESPHome Add-On installed and you have to "Adopt" the ratgdo into ESPHome then click the Edit button which lets you alter the device's configuration and which YAML file to source.

mikekay1, 2023-11-02:
Hey man, thanks for the quick response. Default being

Tx:gpio16
Rx:gpio21
Obstruction:23

Are you saying using the default without switching thr boardtype or gpio (leaving it as d4)?

mikekay1, 2023-11-02:
I will to a massive commit about how to get this running once I get this working, I work professionally in the field IT and electronics and somehow failing the basics. going to continuity test the mosfets and make sure none of them are shorted open. Im almost postitive I have everything right, and now my questions are just seeming to be almost dumb because I dont know where the disconnect is.

mikekay1, 2023-11-02:
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

If running v2.5 are we still following the wiring diagram of 2.0? we only have one obstruction wire. Also my garage door is security 2.0+ so I dont mind the v2 firmware. Ill post back once I check the mosfets

sanjay900, 2023-11-02:
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

With ESPHome, there is no difference betwen v2.5 and v2.0 besides that one pin change, as the Security 1.0+ stuff hasn't made it to ESPHome yet.

mikekay1, 2023-11-02:
Thanks @sanjay900, upgrading is as easy as changing the yaml and then redeploying the yaml correct? Im not aure which version I am on. I used the esphome web installer and flashed 2.0, after I changed the pinouts and made edit to package for v25 firmware. We are still using the wiring of v2.0 board correct red to red, black to obstruction sensor, and white to other side of obstruction sensor.

Continuity on mosfets is fine :(

sanjay900, 2023-11-02:
> Thanks @sanjay900, upgrading is as easy as changing the yaml and then redeploying the yaml correct? Im not sure which version I am on. I used the esphome web installer and flashed 2.0, after I changed the pinouts and made edit to package for v25 firmware. We are still using the wiring of v2.0 board correct red to red, black to obstruction sensor, and white to other side of obstruction sensor.
>
> Continuity on mosfets is fine :(

Yeah, that sounds right for the pins to use. Could you get a clearer photo of your breadboard, just want to confirm the wiring.

sanjay900, 2023-11-02:
If it helps, here's a photo of my working breadboard
![Uploading 20231103_122752.jpg…]()

mikekay1, 2023-11-02:
Its not my camera that is blury its the same lettering on these knock off esp32's. So v25 uses pin gpio16 correct. And with the wall panel button, the white cable goes directly into GDO.

Cant post picture on mobile one sec let me hop on the computer

mikekay1, 2023-11-02:
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

sanjay900, 2023-11-02:
> So v25 uses pin gpio16 correct. And with the wall panel button, the white cable goes directly into GDO.

Ah, other way around, v20 uses GPIO16, v25 uses GPIO22

mikekay1, 2023-11-03:
> > So v25 uses pin gpio16 correct. And with the wall panel button, the white cable goes directly into GDO.
>
> Ah, other way around, v20 uses GPIO16, v25 uses GPIO22

So you are running v20 right, cant really see the resistor divider at d23 but pretty sure our ciruits are the exact same.

Kaldek, 2023-11-03:
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

I forgot that for ESP32 we started recommending using v2.0 YAML settings due to all the pin mapping "fun" that the other folks went through.

https://github.com/Kaldek/rat-ratgdo/blob/main/Supported%20Boards.md#esp-32-based-boards

mikekay1, 2023-11-03:
@Kaldek thanks for chiming in mate, everything with the board is 1:1 to your working prototype. Im wondering if wiring to GDO is incorrect? I know the black wire at GDO side in picture leads to "R" terminal on wall panel.

sanjay900, 2023-11-03:
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

Correct, i am using v20. I also looked at your breadboard and it all seemed the same.

Wait a second, what did you say you did for your wiring?

Kaldek, 2023-11-03:
> @Kaldek thanks for chiming in mate, everything with the board is 1:1 to your working prototype. Im wondering if wiring to GDO is incorrect? I know the black wire at GDO side in picture leads to "R" terminal on wall panel.

Does this help?
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

Kaldek, 2023-11-03:
Umm @mikekay1 why is your Wroom32 GND pin not connected to GND?

sanjay900, 2023-11-03:
oh wow that would do it haha

Kaldek, 2023-11-03:
Yeah ya know...
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

mikekay1, 2023-11-03:
> Umm @mikekay1 why is your Wroom32 GND pin not connected to GND?

Oh but it is at the top left of breadboard then junped back to other side of the breadboard rail.

sanjay900, 2023-11-03:
> > Umm @mikekay1 why is your Wroom32 GND pin not connected to GND?
>
> Oh but it is at the top left of breadboard then junped back to other side of the breadboard rail.

Ah yeah I see it now, it was hidden behind one of the other wires

mikekay1, 2023-11-03:
All good these are a pain in the ass to photograph. I have 4 terminals on GDO. Red T1, White T2, White/Grey T3, and Black T4. Red to Red, Black to Black does white connect to T2 or T3. Which is ground. That might be my problem...

Kaldek, 2023-11-03:
> > Umm @mikekay1 why is your Wroom32 GND pin not connected to GND?
>
> Oh but it is at the top left of breadboard then jumped back to other side of the breadboard rail.

Weird, the pinouts I found for the WROOM 32 don't have that GND pin on them, hence why I didn't look up there.

sanjay900, 2023-11-03:
Yeah, that esp32 pinout was different to mine and that threw me off as well

mikekay1, 2023-11-03:
Maybe its mislabeled! I could try another ground while you confirm the terminal question above.

Kaldek, 2023-11-03:
> All good these are a pain in the ass to photograph. I have 4 terminals on GDO. Red T1, White T2, White/Grey T3, and Black T4. Red to Red, Black to Black does esp32 white wire connect to T2 or T3. Which is ground? That might be my problem...

I believe both of those are GND.  One is the GND for the wall controller and the other is the GND for the obstruction sensors.  I would use T2 for GND.

mikekay1, 2023-11-03:
Yea right eh? This is driving me nuts. Thanks for the help by the way. I couldnt have done it on my own.

My board is this one, not sure if that helps at all.
https://esphome.io/devices/nodemcu_esp32.html

Maybe the fact that the T3 GND is acting as different circuit is messing it all up. Let me try and swap that over. Also the ground on the breadboard. GND should be shared on 3.3v rails and 5v rails... But incase it isnt.

Let me post back in a little bit
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
Kaldek, 2023-11-03:
> > Have you tried just straight up deleting your current board from esphome, and then flashing 2.0 again from scratch using the web flasher?
>
> Collisions are detected even when there was nothing attached, fresh flash. Is there a need to customize the YAML after flashing or does the schematic take into account the GPIO 'translations' automagically?

Collisions, as per the C++ code, mean that the GPIO pin for RX is Low.  Pulled Low, or set Low, doesn't matter, it's Low.

mikekay1, 2023-11-03:
you think something about the board makes it incompatible because it boots that pin low? At this point I'm now ready to buy a d1 mini... I could have bought 20 of these damns boards if I had instead worked a second job lol. I'm guessing I would have to customize my own YAML at this point and try and find which pin is low at boot, and alter it...

Kaldek, 2023-11-03:
> you think something about the board makes it incompatible because it boots that pin low? At this point I'm now ready to buy a d1 mini... I could have bought 20 of these damns boards if I had instead worked a second job lol. I'm guessing I would have to customize my own YAML at this point and try and find which pin is high at boot, and alter it...

It's not about which pins are high at boot, it's about which pins that the code is setting to use as TX and RX, followed by whether the wiring at the circuit level (e.g., the MOSFETs) is wired incorrectly and pulling the line low.

And my statements before are backwards.  Sorry, it's Friday and my brain is already in IDGAF mode.  Let me update that comment.

sanjay900, 2023-11-03:
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

Ill admit i had trouble with this too for a while, but i wrapped my head around it eventually. The serial pin is always held at 12v until either device wants to signal, so the ESP32 assumes if the RX pin is low, that something is trying to write, hence, collision

Kaldek, 2023-11-03:
Everyone needs to ignore what I'm saying at the moment as my brain has just decided to stop functioning for the week and I'm saying gibberish which is probably backwards.

mikekay1, 2023-11-03:
Have a good Friday lads, we are at almost midnight on Thursday here in GMT-4. Regardless, I will try to connect red wire and see if the messages go away. Unless I got a big batch of failed 2n7000s i cant picture anything else being wrong. Was really hoping the T2 to GND would have fixed it but nope. Now truly wonderin if the breadboard would get the same problems if wired to a wemos d1 mini...

sanjay900, 2023-11-03:
> Have a good Friday lads, we are at almost midnight on Thursday here in GMT-4. Regardless, I will try to connect red wire and see if the messages go away. Unless I got a big batch of failed 2n7000s i cant picture anything else being wrong. Was really hoping the T2 to GND would have fixed it but nope. Now truly wonderin if the breadboard would get the same problems if wired to a wemos d1 mini...

Haha I'm sitting here in GMT+13, I don't think your problem is specifically the esp32, but I'm also unsure what the problem actually is.

mikekay1, 2023-11-03:
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

This seems like a good idea, RX by color coding is white. So just the white white with no Red attached

Or

White and red attached to GDO?

Will test tomorrow a bit tired of this myq drama.

Thanks all for all the help!!

mikekay1, 2023-11-09:
tried changing the pins, tried everything even with changing the pins something is just not working right, ordered a weemos if its not that its a bad 2n7000 batch which will all be getting send back. Anyone have a amazon canada link to the right ones I feel like I may have bought something different?

In conclusion I am a complete idiot. As I go to post the link I find out these are LM35/LM35DZ in a TO-92 package :'( [link](https://www.amazon.ca/dp/B07HQCVVFH?psc=1&ref=ppx_yo2ov_dt_b_product_details)

what a gremlin... guys I've been using a bloody temperature sensor the entire time... after this ticket is closed can we delete it for ever and pretend none of this ever happened?

new parts on order... I figured there was something very very wrong. I've designed a ton of these circuits before. will keep everyone posted!

Kaldek, 2023-11-10:
All good mate, we've all been there!!!!

mikekay1, 2023-11-11:
Still not working able to close and open door, but not get status, or trigger light on/off. Going to buy a weemos and post back

mikekay1, 2023-11-18:
Bought a weemos, reflashed it and rebuild everything what else can I do... I am at my whits end with this thing.

Any help, should I solder everything

Closed 2023-11-11.

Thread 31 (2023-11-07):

Can see logs and statuses but cannot control the garage door

phutchins, 2023-11-07:
I've built the circuit with an ESP8266 Mini D1 on a breadboard based on the schematic and breadboard picture. I've flashed it with the Esphome ratgdo (https://ratgdo.github.io/esphome-ratgdo/). I can access the web UI and see logs going through if I open/close the garage door with MyQ. The statuses update, like the motion, obstruction and open/closed status.

When I click the toggle door button, light, or door up/down buttons, it doesn't work. In the logs I see 'Toggle door' Pressed. Then the 'Rolling code counter', then saving preferences to flash. A little bit later I'll see a Status: door=CLOSED light=OFF lock=UNLOCKED showing that the door has not moved or changed.

Any ideas on where to start looking?

It might be hard to see but I've attached a picture of the board. Also attaching a screenshot of some logs showing the end of where I closed the door with the MyQ app, then an attempt at opening it through HomeAssistant.

Garage Door: Chamberlain B4613T
Board: ACEIRMC ESP8266 [[link](https://a.co/d/fldpaNH)]

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

Kaldek, 2023-11-07:
This means your TX line isn't working.   Which board did you click when you flashed it?
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

phutchins, 2023-11-07:
Ah, yeah, I clicked the top left one because it said ESP8266. I just re-flashed it and set it up again in HA. After flashing it, I moved it back to the bread board and booted it up. It was seeing updates from the garage door again but still didn't open/close it. I rebooted it and now it is really slow to load the web interface. Might the wiring or some lack of configuration be causing the extreme slowness? I.E. it still hasn't loaded the full UI and its been 5 or so minutes.

phutchins, 2023-11-07:
I added the ESPHome addon to HomeAssistant and validated the node which pulled the config. I verified that I have the wires connected to the correct pins on the board itself (like tx, rx, and obst). Its loading faster now so maybe it was just doing something but still no luck with opening/closing.

Is there something I need to do with getting the current rolling code and syncing? I can't seem to find any helpful info on how to do that but I might be missing something.

phutchins, 2023-11-07:
Could it be an issue with the second transistor? I have the RFP30N06LE MOSFET but switched to using both of the small ones as that was what was in the picture to see if I could get it working.

Kaldek, 2023-11-07:
> Is there something I need to do with getting the current rolling code and syncing? I can't seem to find any helpful info on how to do that but I might be missing something.

Worst-case you need to ask it to Sync using the "Sync" button on the web interface.

Also make sure your device is a Security+ 2.0 model by checking over on the original ratgdo project repo.

You can also try swapping your MOSFETs around.  If you get "Collision detected" messages or just can't receive (but can transmit now) then that MOSFET is bad.

phutchins, 2023-11-07:
I've tried the sync button a few times with no luck either. I looked up the garage door opener and confirmed that it is a Security+ 2.0 model. I'll try swapping the MOSFETs.

Here is the first chunk of config just in case that helps at all...

`INFO Detected timezone 'America/New_York'
substitutions:
  id_prefix: ratgdov25
  friendly_name: ratgdov2.5 ff7723
  uart_tx_pin: D1
  uart_rx_pin: D2
  input_obst_pin: D7
  status_door_pin: D0
  status_obstruction_pin: D8
  dry_contact_open_pin: D5
  dry_contact_close_pin: D6
  dry_contact_light_pin: D3
  name: ratgdov25-ff7723
esphome:
  name: ratgdov25-ff7723
  friendly_name: ratgdov2.5 ff7723
  name_add_mac_suffix: false
  project:
    name: ratgdo.esphome
    version: '2.5'
  build_path: build/ratgdov25-ff7723
  platformio_options: {}
  includes: []
  libraries: []
  min_version: 2023.10.6
esp8266:
  board: d1_mini_lite
  restore_from_flash: true
  framework:
    version: 3.0.2
    source: ~3.30002.0
    platform_version: platformio/espressif8266@3.2.0
  early_pin_init: true
  board_flash_mode: dout
preferences:
  flash_write_interval: 5s
external_components:
- source:
    url: https://github.com/ratgdo/esphome-ratgdo
    type: git
  refresh: 1s
  components: all
ratgdo:
- id: ratgdov25
  input_gdo_pin:
    number: 4
    mode:
      input: true
      analog: false
      output: false
      open_drain: false
      pullup: false
      pulldown: false
    inverted: false
  output_gdo_pin:
    number: 5
    mode:
      output: true
      analog: false
      input: false
      open_drain: false
      pullup: false
      pulldown: false
    inverted: false
  input_obst_pin:
    number: 13
    mode:
      input: true
      analog: false
      output: false
      open_drain: false
      pullup: false
      pulldown: false
    inverted: false`

phutchins, 2023-11-08:
Swapping the MOSFETs didn't make any difference. Anything I can do to test the outputs/inputs of the circuit to tell if its doing the right things?

phutchins, 2023-11-08:
The red wire going to the garage door opener does both the status updates for things like motion as well as commands from the ESP to open/close the door and such, correct? If thats true, then maybe the transistors aren't doing their job and setting up the line for communication?

Kaldek, 2023-11-08:
> The red wire going to the garage door opener does both the status updates for things like motion as well as commands from the ESP to open/close the door and such, correct? If thats true, then maybe the transistors aren't doing their job and setting up the line for communication?

There's no real setup going on.  The red wire from the GDO is +12v all the time unless something is transmitting (whether that is the GDO itself, the wall controller, or the ratgdo).  Any time something wants to transmit, it does this by pulling the +12v (red wire) to ground in pulses at 9600 bits per second (9600 pulses per second).  The RX MOSFET sees this as switching the MOSFET **off** for each pulse, which the D2 pin on the ESP module sees as brief pulses (at 9600 bps) of +3.3v.

As for the TX side of the ESP, pin D1 is not doing anything unless it wishes to transmit, at which point it will send +3.3v pulses (at 9600 BPS) to the gate of the TX MOSFET.  Each pulse will cause the +12v line (red wire) to get pulled to ground, which all other devices on the wire can detect as transmission data.

If you have an oscilloscope, what you need to do is monitor both pin D1 directly and look for +3.3v pulses when you try to transmit (e.g., open the door, query status, etc), and if that's working you need to monitor the red wire and look for inverted pulses from +12v to ground when you try to transmit.  That will tell you where the problem lies.

Also, try connecting the 3V3 pin of the ESP module to pin D1 and hold it there.  If the MOSFET is working the +12v line (red wire) will be pulled to Ground and your wall controller should switch off.

Kaldek, 2023-11-08:
I'm also starting to wonder if some of the weirdness people are seeing when using the 2n7000 is due to their particular variant of the 2n7000 not switching reliably at 3.3v.  Again, an oscilloscope can validate this.

sanjay900, 2023-11-08:
> I'm also starting to wonder if some of the weirdness people are seeing when using the 2n7000 is due to their particular variant of the 2n7000 not switching reliably at 3.3v. Again, an oscilloscope can validate this.

I even found i had problems when using it on a breadboard, but not when i built a PCB, though i very possibly swapped transistors when i moved to the PCB so it could be that as well.

phutchins, 2023-11-08:
First thing I tried was connecting the 3V3 pin of the ESP to pin D1 which in fact did NOT switch the wall controller off. I assume that this means there is an issue with the setup or MOSFET.

I'm working through your explanation to see if I can troubleshoot with the oscilloscope. I'll get back to you with my findings there soon! I greatly appreciate the help. I feel like I'm close...

Kaldek, 2023-11-08:
> First thing I tried was connecting the 3V3 pin of the ESP to pin D1 which in fact did NOT switch the wall controller off. I assume that this means there is an issue with the setup or MOSFET.

Yeah sounds like your TX circuit is not pulling the red wire to ground at all.

Kaldek, 2023-11-08:
I made a video on how to test this:
https://www.youtube.com/watch?v=AlZNbD49sbE

phutchins, 2023-11-09:
@Kaldek , thanks so much for this video. I'm not sure what was wrong with my initial setup but I went through it all again, replaced the MOSFETs, tested based on your very helpful description above, and now it works! On my bench I was able to get continuity between the two sides of the tx MOSFET so I hooked it back up and it works!

I'm starting to put it on the pcb so I can have a permanent solution. I'll share pics when it's done!

Kaldek, 2023-11-09:
Awesome news mate!

Kaldek, 2023-11-09:
@phutchins I'll close thise but you can share your pics here when you're done.

Closed 2023-11-09.

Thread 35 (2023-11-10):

8500C and 2x 2n7000 MOSFETs doesn't seem to be working.

dorkage, 2023-11-10:
I have a jackshaft 8500C with a Yellow Learn button and 888LM wall panel.

I built a protoboard today following the latest schematics, I had gotten the IRLB8721 before it was know they were not suitable, so I went with 2x 2n7000.

When flashing to native RATGDO opener for Board V2.5 and going with Security+ 1.0, nothing seems to work. If I switch to Security+ 2.0 I see more things in the logs, but no commands work.

With Security+ 1.0

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

No commands trigger anything.

Switching to 2.0

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

Rolling codes seem to do more, but I don't have any action from the opener for any functions. I used RAT-RATGDO V6 for D1 Mini and the native RATGDO firmware. Perhaps I need to change to the ESP Home firmware, but I was under the impression my opener was Security+ 1.0. What should I try next?

mikekay1, 2023-11-10:
I believe the esphome firmware does have security 1.0+

Yellow button ahould mean security 2.0+ double checked the gpio, resistor types and mosfet to make sure everything is correct?

mikekay1, 2023-11-10:
Have you tried syncing the rolling codes? I think those logs mean it communicating.

dorkage, 2023-11-10:
Thanks for the quick reply.

I double checked it visually a few times, but I'll bring home a Fluke87 this weekend and make sure.

As far as the version of security plus, the jackshaft openers usually fall under 1.0. Mine garage door will open if I short the remote wires.

Kaldek, 2023-11-10:
Can't really speak for v1.0 at the moment as everybody building a board for a GDO which is Security+ 1.0 doesn't seem to have much luck.

For MOSFET testing, you can follow this video I made.  I would guess in your case if your MOSFET circuit is working, this test will toggle your garage door.

https://youtu.be/AlZNbD49sbE

mikekay1, 2023-11-10:
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

Ah okay yea, shorting the wires is a def security 1.0 then.

This is all my google fu was able to find.

dorkage, 2023-11-10:
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

I'll try this this weekend. I suspect in my case this would cause the door to open.

> Have you tried syncing the rolling codes? I think those logs mean it communicating.

I am not having luck finding out how to sync the rolling codes on either here or the official RATGDO page, any links?

rlowens, 2023-11-10:
> I am not having luck finding out how to sync the rolling codes on either here or the official RATGDO page, any links?

This is from a comment I read:
> Changing the client_id is like starting fresh from the GDO's point of view (it doesn't matter what the rolling code is when you change the client_id, but once you send the first command, the rolling code can only increase from that point on).

> When you change the client_id is normal for the first command to be ignored, but the following ones should start working. A simple test is change the client_id and toggle the light from Home Assistant a couple times and it should toggle the GDO light. If that doesn't work, you have something wrong with the wiring.

So, just change the client_id and give it a try I think.

dorkage, 2023-11-10:
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

Again, I am not finding any information on how to do this.

Kaldek, 2023-11-11:
> Again, I am not finding any information on how to do this.

Apologies mate, but most of us are as much in the dark as you are.  You could try asking on the official ratgdo repo but as soon as Paul finds out you're using a self-made one you may even be banned from posting there.  I've been banned already, but I mean, he's probably pissed that I created an open-source schematic. 😬

Kaldek, 2023-11-14:
Closing due to lack of updates from OP.

Closed 2023-11-14.

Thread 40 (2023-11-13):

A companion device for door close alerts from automations

CrazyCoder, 2023-11-13:
Just to document my little project. It's ESPHOME esp2866 simple device with a buzzer and 4x4 WS2812 LED matrix I use to alert when any automation is about to close the door.

ESPHOME config: [gdalert.yaml](https://gist.github.com/CrazyCoder/cafb68fbc308315d7ad1a71da998df72).

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

Bottom shield is completely optional, and I use it only for mounting with a Velcro-like adhesive tape. You can opt for a custom 3D-printed enclosure or your own creative way of attaching it to a surface.

BOM:

- [ESP8266 D1 Mini](https://www.amazon.com/Organizer-ESP8266-Internet-Development-Compatible/dp/B081PX9YFV/)
- [x2 proto shields for D1](https://www.amazon.com/gp/product/B07L756KQS/)
- [Active buzzer module](https://www.amazon.com/gp/product/B07GDMV5DB/) (use 3.3V for VCC and D5 for control, inverted)
- [4x4 WS2812 matrix](https://www.amazon.com/CANADUINO-Matrix-Fully-Addressable-WS2812B/dp/B07LDYDDSZ/) (controlled via RX pin)

You can use any 5V addressable LED strip/matrix/etc, but this one was easy to mount and looks nice.

Trigger a switch from Home Assistant automation. 5s and 10s switches turn off automatically after the specified time. You can control the light and buzzer independently.

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

Kaldek, 2023-11-15:
If you would like this content added to the repo as an optional addition, let me know.

Closed 2023-11-15.

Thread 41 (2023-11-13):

Issue with 2N7000

ripnet, 2023-11-13:
I wanted to provide feedback on three GDOs that I've installed.

The first has a [050DCTWF](https://www.chamberlain.com/receiver-logic-board-dc-wifi/p/050DCTWF) logic board, and this works well two 2n7000's.

The other two have [050DCTBLK](https://www.liftmaster.com/logic-board-bluetooth-enabled-lock/p/050DCTBLK) logic boards, and will not work when using a 2n7000 on the transmitter. I ended up using [IRLB8721PbF](https://www.digikey.com/en/products/detail/infineon-technologies/IRLB8721PBF/2127670) FETs on those, and they are working.

I'm not entirely sure why the logic board would make the difference with how my ESPs would switch transistors.

I know this isn't an issue per se, but I thought the community might benefit from my experience. Apologies if this isn't the forum for this.

Kaldek, 2023-11-14:
Weird.  As far as we know, the IRLB8721's weren't working at all for others.

This might well be why Paul Wieland uses an AO3400A as it might bridge the gap between the two extremes.

TaylorTWBrown, 2023-11-14:
Very interesting. Thanks for the insight - I'm having trouble getting my transmission to work as well, and I have the same chamberlain.

However, I'm also only using 1k resistors while I wait for higher values to arrive.

Can you comment on the factors that make some npn transistors more suitable than others for this application?

Kaldek, 2023-11-14:
> Can you comment on the factors that make some npn transistors more suitable than others for this application? Essentially, we've built a half-duplex logic voltage shifter, right?

The ESP8266 needs to switch the red wire to ground via a 3.3v trigger to the gate (for TX).  Therefore a MOSFET that can switch based on that voltage and can handle the +12v Drain to Source is needed.

For RX, a MOSFET is needed that can switch off when the +12v gets pulled to ground.  So unless there is data being transmitted, the RX MOSFET is always on, which pulls the RX pin of the ESP8266 to ground (Drain to Source).

Those are the requirements.

It is a half duplex voltage shifter but it's inverted both for RX and TX.

Closed 2023-11-15.

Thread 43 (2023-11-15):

Sec+1 and two 2N7000 not working

tronikos, 2023-11-15:
See `https://github.com/PaulWieland/ratgdo/issues/243` for my issue including equipment and logs.

I have checked the circuit several times and it seems correct.

Steps I have done to troubleshoot:

Multimeter at continuity mode between red and white wires: D of Q2 (or G of Q1) and S of Q2 (or S of Q1) no sound while ratgdo is booting. After a few unsuccessful attempts of “Looking for security+ 1.0 wall panel...” it resulted in “No wall panel detected. Switching to emulation mode.” and then there was some rhythmic chirping sound on the multimeter. This indicates to me there was data transmitted over the line. I think the logs (see linked issue above) indicate that too but the status seems to always be reported as open. Applying 3.3V to D1 (G of Q2) there was a continuous sound on the multimeter meaning the 2N7000 Q2 used for TX was successful in pulling its D to the ground and the door opened.

Multimeter at continuity mode between D2 (D of Q1) and GND (S of Q1): high frequency chirping sound while ratgdo firmware was running. Applying 3.3V to red wire (G of Q1) continuous sound. This suggests 2N7000 Q1 is also working? I tried this on my bench. Is it worth trying it again connected to the GDO which has 16V instead of 3.3V?

Multimeter at continuity mode between D1 (G of Q2) and GND (S of Q2): continuous sound while booting and then low frequency chirping sound after “No wall panel detected. Switching to emulation mode.”.

Do you have any suggestions how to troubleshoot this further? Do my tests confirm wiring is correct and the two 2N7000 are working as expected? Is there any point trying a different transistor?

Kaldek, 2023-11-15:
Hi mate, we're lacking someone who has stated they have a working open source board using a Security+ 1.0 system.  Without that, and given the code is maintained by Paul Wieland, we're unable to help.

Your best bet is to buy a board from Paul and wait for delivery.  If there are issues after that which are related to the code, he will likely assist.

Kaldek, 2023-11-28:
Closing due to lack of updates.

Closed 2023-11-28.

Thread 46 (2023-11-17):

IMPORTANT!!! - PCB boards/gerber files for all boards except D1 mini - 8266 prior to 11/17/23 have White and Black silkscreen swapped!

bjhiltbrand, 2023-11-17:
I was made aware of, and fixed an issue where the silkscreen that I had placed on most boards in the kicad files folder (the D1 mini - ESP32, ESP32-Wide, and Bare 8266 boards) had the terminal for the white wire (ground) swapped with the terminal for the black wire (obstruction sensors). Please note that if you have had boards manufactured prior to today, that the silkscreen is incorrect, and you will need to make note of this when connecting your wires. I apologize for any inconvenience this causes.

@Kaldek, please review and approve this pull request as soon as you can. Thank you.

https://github.com/Kaldek/rat-ratgdo/pull/45

dolfelt, 2023-11-18:
Thanks for the fix @bjhiltbrand!

Kaldek, 2023-11-20:
Approved and merged but maybe @rlowens did it as my weekend memory is fuzzy.

Closed 2023-11-20.

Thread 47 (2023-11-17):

I can read the door status, but not control it

dpeart, 2023-11-17:
So I built one of my boards with the D1 mini.
I hooked the red, white and black wires to the GDO.

LiftMaster Security + 2.0

I can read the state in HA, motor running, obstruction clear or not and it knows if the door is open or closed.

I cannot control the door at all.  No open, close, light on/off.

ideas?

bjhiltbrand, 2023-11-17:
I went through the schematics again and I think I have them right. If not, I sincerely apologize. Have you taken a look at this issue?

https://github.com/Kaldek/rat-ratgdo/issues/31

@Kaldek also has a video that he did linked at the bottom of that issue to do a little troubleshooting. Also, make sure that you flash the ESPHome firmware for the 2.5 board so the pins match up the way they should.

When I get my boards tomorrow, I'll solder it up and have a shot as well.

dpeart, 2023-11-18:
the gnd pin on the D1 Mini is not connected to ground.  It is in my PCB in Ki-CAD, checking with JLCPCB now to see what happened.

dpeart, 2023-11-18:
Sure enough.  When JLCPCB read it in it got messed up.

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

dpeart, 2023-11-18:
KiCad
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

dpeart, 2023-11-18:
I'll blue wire it and see if that fixes the issue.  I can see that it would be difficult to ground the red wire if your grounds are different

bjhiltbrand, 2023-11-18:
Interesting. Well, now that they messed up, can you get an updated board with a good silkscreen for free? ;) I don't know if anyone here has a solid grasp of KiCAD (you or @dolfelt probably do for sure), but if they do, it might be a good idea to review all the designs to make sure I didn't screw stuff up.

dpeart, 2023-11-18:
KiCad is fine.  Just need to figure out what happened

dpeart, 2023-11-18:
Yep, grounding pin 10 and everything works.  Grounding is as the entire back plane is ground

maskedpirate, 2023-11-29:
@dpeart - I'm having the same issue of only being able to read status but not control it with my esp32 variant. In my case the obstruction sensor is never updated either; only door, light, rolling code, etc.

I used the kicad PCB files from this repo and exported all the relevant files with the JLCPCB plugin and had them assemble the components. When you say you grounded pin 10 (GND), do you mean you soldered a wire from the GND pin to the GDO WHT GND? If it matters, I'm powering the ESP32 via USB.

Thanks!

dpeart, 2023-11-29:
My pin 1- (GND) was left floating, so I scraped a bit of the green coating away to expose the ground plane.  I then put a drop of solder to connect the pin to the ground plane.

Closed 2023-11-18.

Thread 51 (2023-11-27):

using a raspberry pi pico w

godmar, 2023-11-27:
This is more of a discussion question, so feel free to close this issue.

It seems like the hardware schematics would be compatible with a RPi Pico W, wouldn't it?  Has anyone tried that? Would a Pico be more likely to work with the existing 12V power if it drew less current?

I'm also a bit confused about what's open source. Apparently, this project reverse-engineered the ratgdo board and put different software on it.  I understand that the GDO uses some kind of serial protocol that the microcontroller reads - what protocol is this and where is the code for it?  At first glance, I didn't see it in either this repo or in the ratgdo repo - but I may have missed it?

Thank you.

Kaldek, 2023-11-27:
> I'm also a bit confused about what's open source

Well, the original ratgdo project is itself open source, hence the ESPHome fork.  However the board design was closed source, so this repo is really just an open source design either for using modules (like the Wemos D1 Mini or the ESP 32 WROOM), or using a bare ESP8266.  It gets you the necessary circuitry to interface with the GDO.

rlowens, 2023-11-27:
Yes, this could work on a rp2040 mcu (the mcu in the RPi Pico W), and the esphome firmware might even work without changing much at all since esphome supports rp2040 already.

As far as running off of the 12V power, I don't know.

Re: open source: The software for ratgdo is at https://github.com/ratgdo:
https://github.com/ratgdo/mqtt-ratgdo is the (original) mqtt firmware written in c++ for Arduino I think? it uses https://github.com/ratgdo/secplus (written in c) and https://github.com/ratgdo/espsoftwareserial

https://github.com/ratgdo/esphome-ratgdo is the esphome firmware which uses the above

and the work-in-progress https://github.com/ratgdo/homekit-ratgdo (homekit firmware, not working yet)

This project open-sourced a hardware schematic to interface mcu's running the ratgdo firmware to a GDO without buying the ratgdo hardware sold by Paul Weiland.

Closed 2023-11-28.

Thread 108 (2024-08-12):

880LWM Issue

njschwartz, 2024-08-12:
Wonder if anyone else has experienced something similar.  I have the 88LWM connected to my Jackshaft 8500W opener.  I built a prototype ratratgdo using the three resistor/2N7000.  At first I didn't think it was working at all as when I wired it up it wouldn't connect and I could hear a buzzing from the 88LWM switch when I would try to trigger something in ESPHome.  I finally tried disconnecting the switch and only connecting the ratratgdo and it works perfectly. But as soon as I reconnect the wall switch it stops again like the two are interfering with each other.  Is there something I am missing as far as wiring a switch in (I know on the ratgdo from Paul he has a passthrough of some sort on the board.  I am not really clear how I would wire that. Or is this an issue with my build or the 2N7000's maybe?  I would love to hear if anyone else has has this issue and what I might do to troubleshoot it.  I appreciate it!

Kaldek, 2024-09-05:
Generally these are indeed wiring issues and the 12v red wire is being pulled down causing it to not get power.  Identifying exactly what caused this usually means busting out the oscilloscope to confirm the behaviour on that wire and then working backwards from there.

Closed 2024-09-05.

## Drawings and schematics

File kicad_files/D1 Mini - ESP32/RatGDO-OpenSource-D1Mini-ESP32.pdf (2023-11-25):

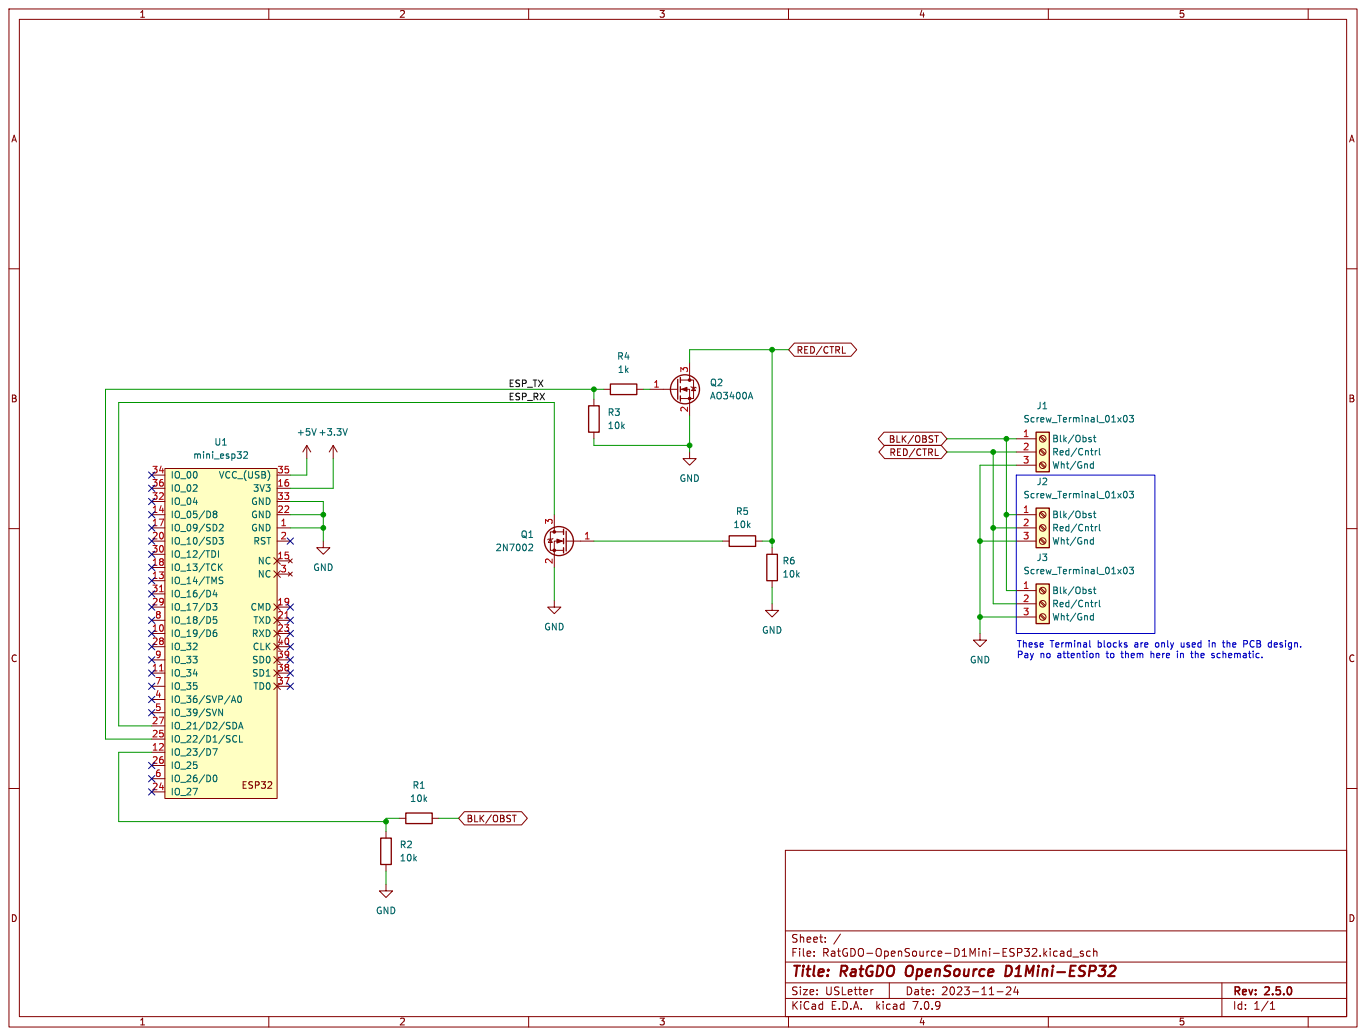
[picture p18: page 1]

J3 Screw_Terminal_01x03 GND
File: RatGDO-OpenSource-D1Mini-ESP32.kicad_sch Sheet: / R6

These Terminal blocks are only used in the PCB design.

Id: 1/1 Title: RatGDO OpenSource D1Mini-ESP32

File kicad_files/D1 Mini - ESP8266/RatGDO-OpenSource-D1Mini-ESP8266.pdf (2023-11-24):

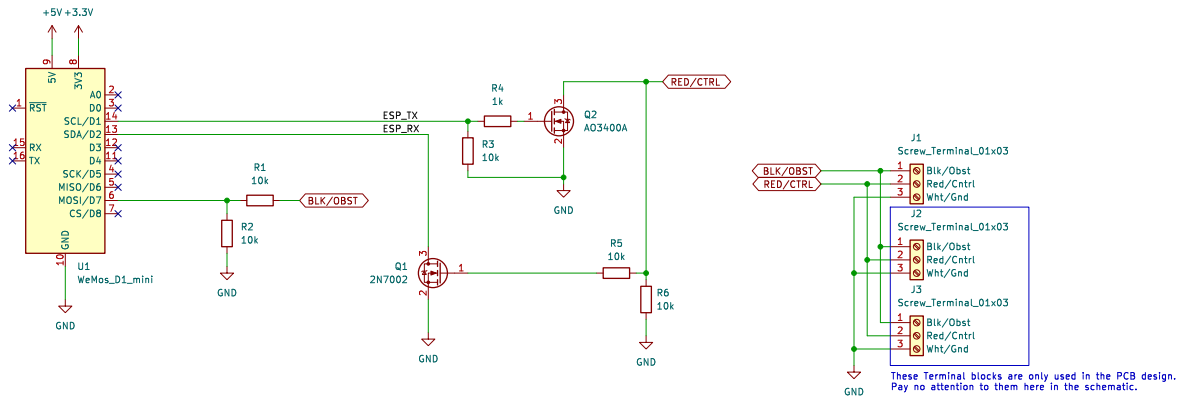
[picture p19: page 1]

9 U1 WeMos_D1_mini Blk/Obst 1 Red/Cntrl 2 Wht/Gnd 3

These Terminal blocks are only used in the PCB design.

File: RatGDO-OpenSource-D1Mini-ESP8266.kicad_sch Sheet: /
Id: 1/1 Title: RatGDO OpenSource D1Mini-ESP8266

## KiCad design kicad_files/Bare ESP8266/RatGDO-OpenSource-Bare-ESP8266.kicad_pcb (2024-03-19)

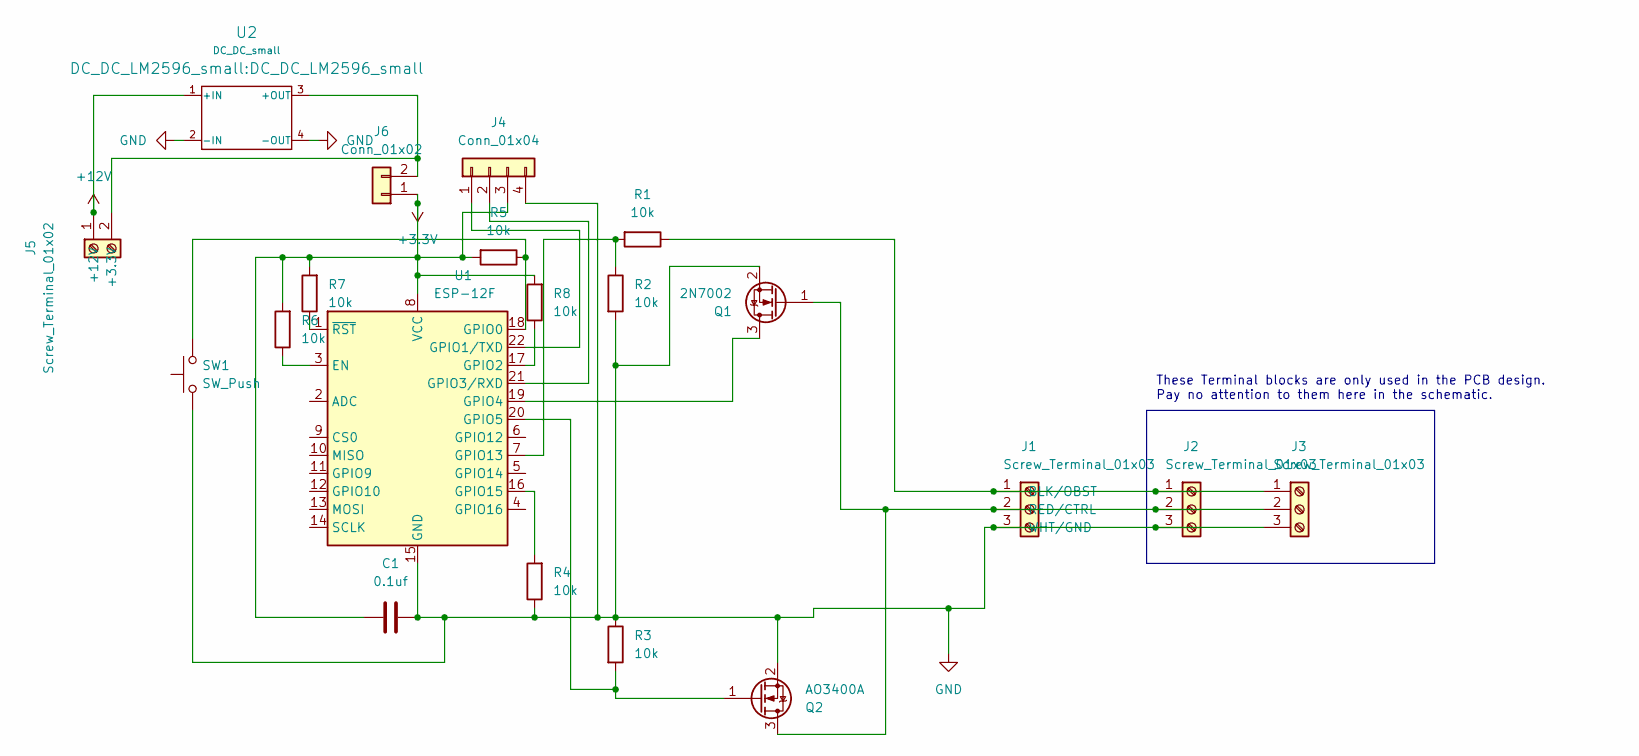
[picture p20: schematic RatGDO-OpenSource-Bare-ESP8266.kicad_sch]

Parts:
C1: 0.1uf; C_0805_2012Metric
J1: Screw_Terminal_01x03; TerminalBlock_Phoenix_MKDS-1,5-3_1x03_P5.00mm_Horizontal
J2: Screw_Terminal_01x03; PhoenixContact_MCV_1,5_3-G-3.5_1x03_P3.50mm_Vertical
J3: Screw_Terminal_01x03; PinSocket_1x03_P2.54mm_Vertical
J4: Conn_01x04; PinSocket_1x04_P2.54mm_Vertical
J5: Screw_Terminal_01x02; TerminalBlock_Phoenix_MKDS-1,5-2_1x02_P5.00mm_Horizontal
J6: Conn_01x02; PinHeader_1x02_P2.54mm_Vertical
Q1: 2N7002; SOT-23
Q2: AO3400A; SOT-23
R1, R2, R3, R4, R5, R6, R7, R8: 10k; R_0805_2012Metric
SW1: SW_Push; SW_SPST_EVQQ2
U1: ESP-12F; ESP-12E
U2: DC_DC_small; DC_DC_LM2596_small

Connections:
+3.3V: C1.1, J4.3, J6.1, R5.2, R6.2, R7.2, R8.2, U1.8 (VCC)
+12V: J5.1 (+12V), U2.1 (+IN)
GND: C1.2, J1.3 (WHT/GND), J2.3, J3.3, J4.4, Q1.2 (S), Q2.2 (S), R2.2, R3.1, R4.1, SW1.1, U1.15 (GND), U2.2 (-IN), U2.4 (-OUT)
unnamed: J1.1 (BLK/OBST), J2.1, J3.1, R1.1
unnamed: J1.2 (RED/CTRL), J2.2, J3.2, Q1.1 (G), Q2.3 (D)
unnamed: J4.1, U1.22 (GPIO1/TXD)
unnamed: J4.2, U1.21 (GPIO3/RXD)
unnamed: J5.2 (+3.3V), J6.2, U2.3 (+OUT)
unnamed: Q1.3 (D), U1.19 (GPIO4)
unnamed: Q2.1 (G), R3.2, U1.20 (GPIO5)
unnamed: R6.1, U1.3 (EN)
unnamed: R5.1, SW1.2, U1.18 (GPIO0)
unnamed: R8.1, U1.17 (GPIO2)
unnamed: R1.2, R2.1, U1.7 (GPIO13)
unnamed: R4.2, U1.16 (GPIO15)
unnamed: R7.1, U1.1 (~RST)

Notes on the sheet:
These Terminal blocks are only used in the PCB design. Pay no attention to them here in the schematic.

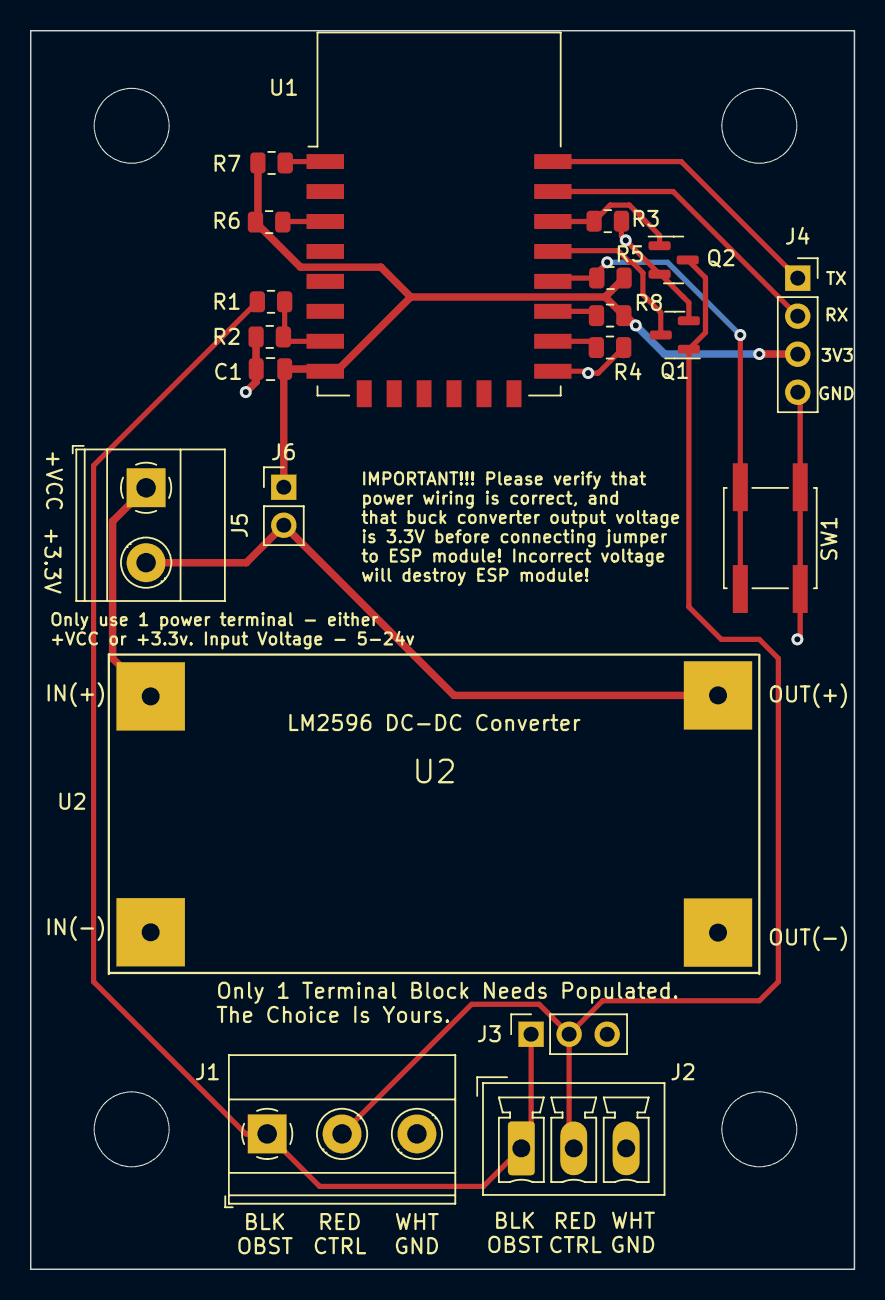
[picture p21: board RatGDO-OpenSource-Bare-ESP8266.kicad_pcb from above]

Board: 2 copper layers, 55.0 x 82.7 mm, 24 parts (0 on the bottom side), 16 nets.

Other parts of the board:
H1, H1#2, H1#3, H1#4: MountingHole_5mm

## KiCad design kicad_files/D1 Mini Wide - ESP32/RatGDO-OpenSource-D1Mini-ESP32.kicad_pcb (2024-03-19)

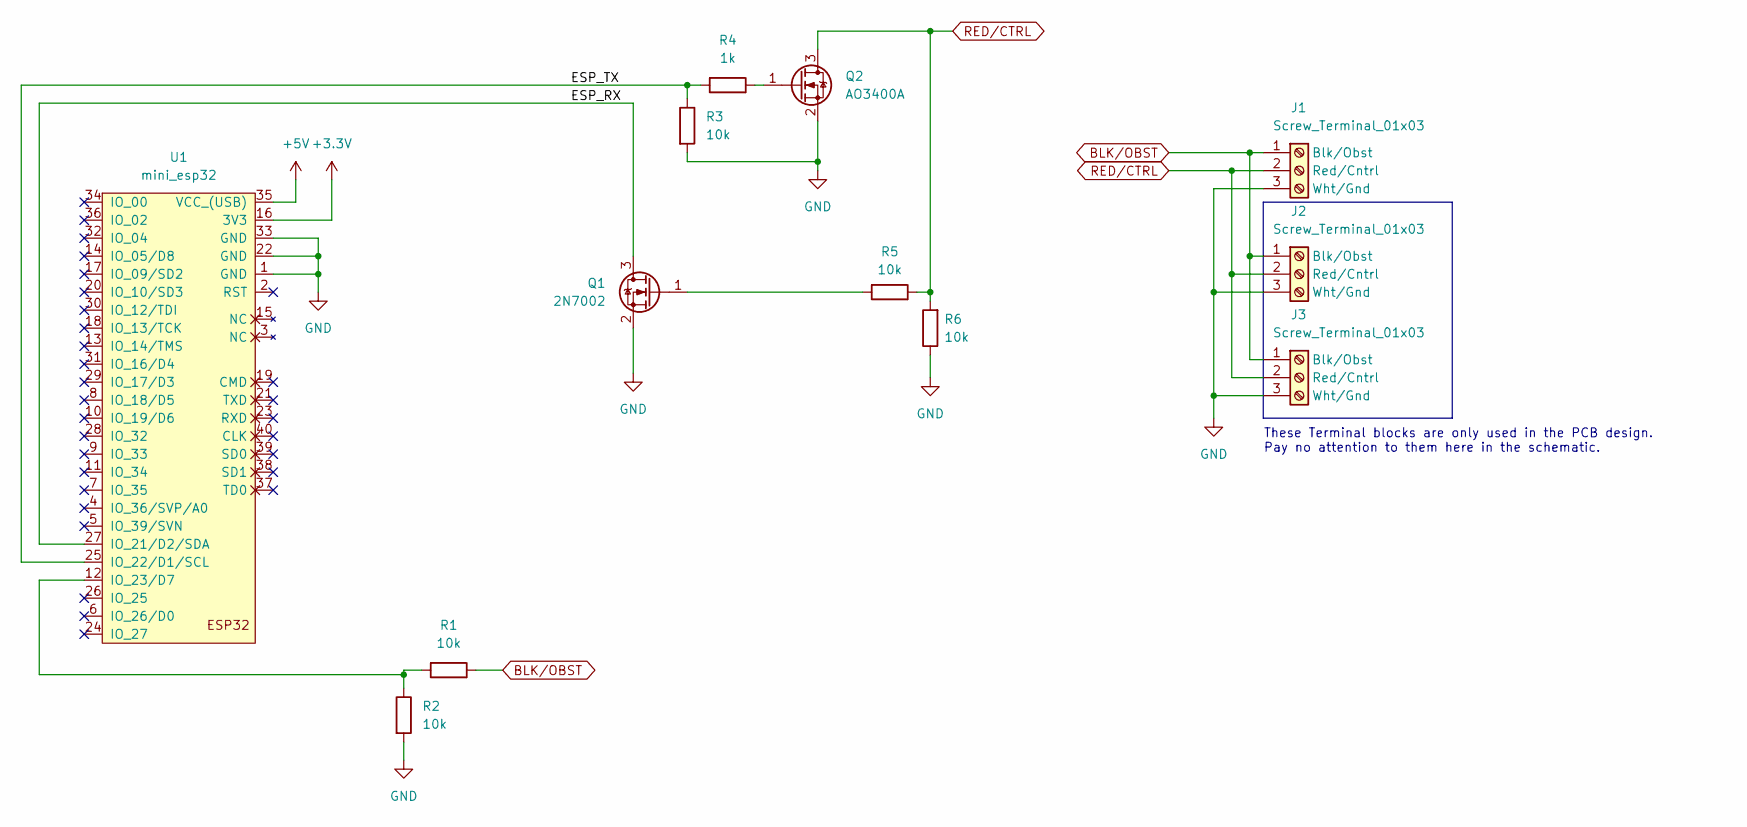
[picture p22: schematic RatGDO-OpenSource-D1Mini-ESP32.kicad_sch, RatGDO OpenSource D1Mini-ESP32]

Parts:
J1: Screw_Terminal_01x03; TerminalBlock_Phoenix_MKDS-1,5-3_1x03_P5.00mm_Horizontal; LCSC# C8483
J2: Screw_Terminal_01x03; PhoenixContact_MCV_1,5_3-G-3.5_1x03_P3.50mm_Vertical
J3: Screw_Terminal_01x03; PinHeader_1x03_P2.54mm_Vertical
Q1: 2N7002; SOT-23_Handsoldering; LCSC# C8545
Q2: AO3400A; SOT-23_Handsoldering; LCSC# C20917
R1, R2, R3, R5, R6: 10k; R_0805_2012Metric_Pad1.20x1.40mm_HandSolder; LCSC# C17414
R4: 1k; R_0805_2012Metric_Pad1.20x1.40mm_HandSolder; LCSC# C17513
U1: mini_esp32; ESP32_mini

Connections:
+3.3V: U1.16 (3V3)
+5V: U1.35 (VCC_(USB))
/ESP_RX: Q1.3 (D), U1.27 (IO_21/D2/SDA)
/ESP_TX: R3.1, R4.2, U1.25 (IO_22/D1/SCL)
BLK/OBST: J1.1 (Blk/Obst), J2.1 (Blk/Obst), J3.1, R1.1
GND: J1.3 (Wht/Gnd), J2.3 (Wht/Gnd), J3.3, Q1.2 (S), Q2.2 (S), R2.2, R3.2, R6.1, U1.1 (GND), U1.22 (GND), U1.33 (GND)
unnamed: Q1.1 (G), R5.2
unnamed: Q2.1 (G), R4.1
unnamed: R1.2, R2.1, U1.12 (IO_23/D7)
RED/CTRL: J1.2 (Red/Cntrl), J2.2 (Red/Cntrl), J3.2, Q2.3 (D), R5.1, R6.2

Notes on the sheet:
These Terminal blocks are only used in the PCB design. Pay no attention to them here in the schematic.

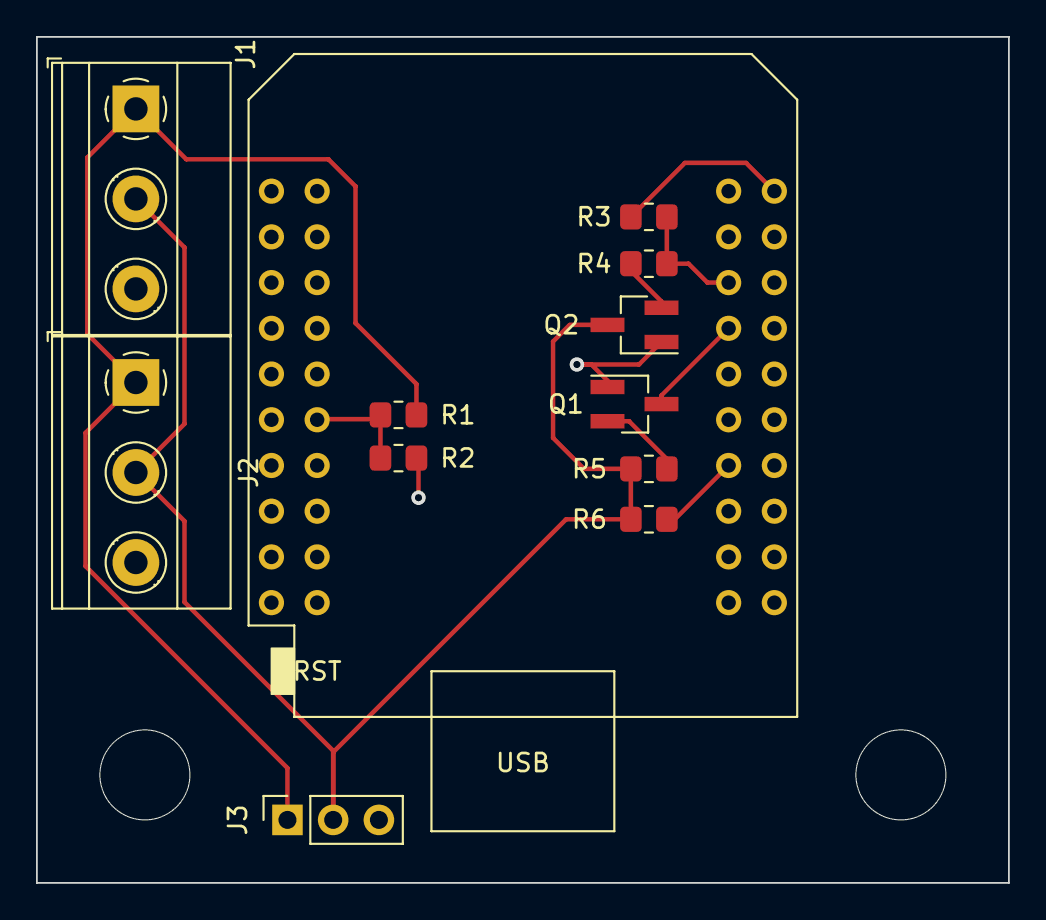
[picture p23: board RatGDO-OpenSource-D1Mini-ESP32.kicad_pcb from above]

Board: 2 copper layers, 54.0 x 47.0 mm, 14 parts (0 on the bottom side), 8 nets.

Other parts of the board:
H1, H1#2: MountingHole_5mm

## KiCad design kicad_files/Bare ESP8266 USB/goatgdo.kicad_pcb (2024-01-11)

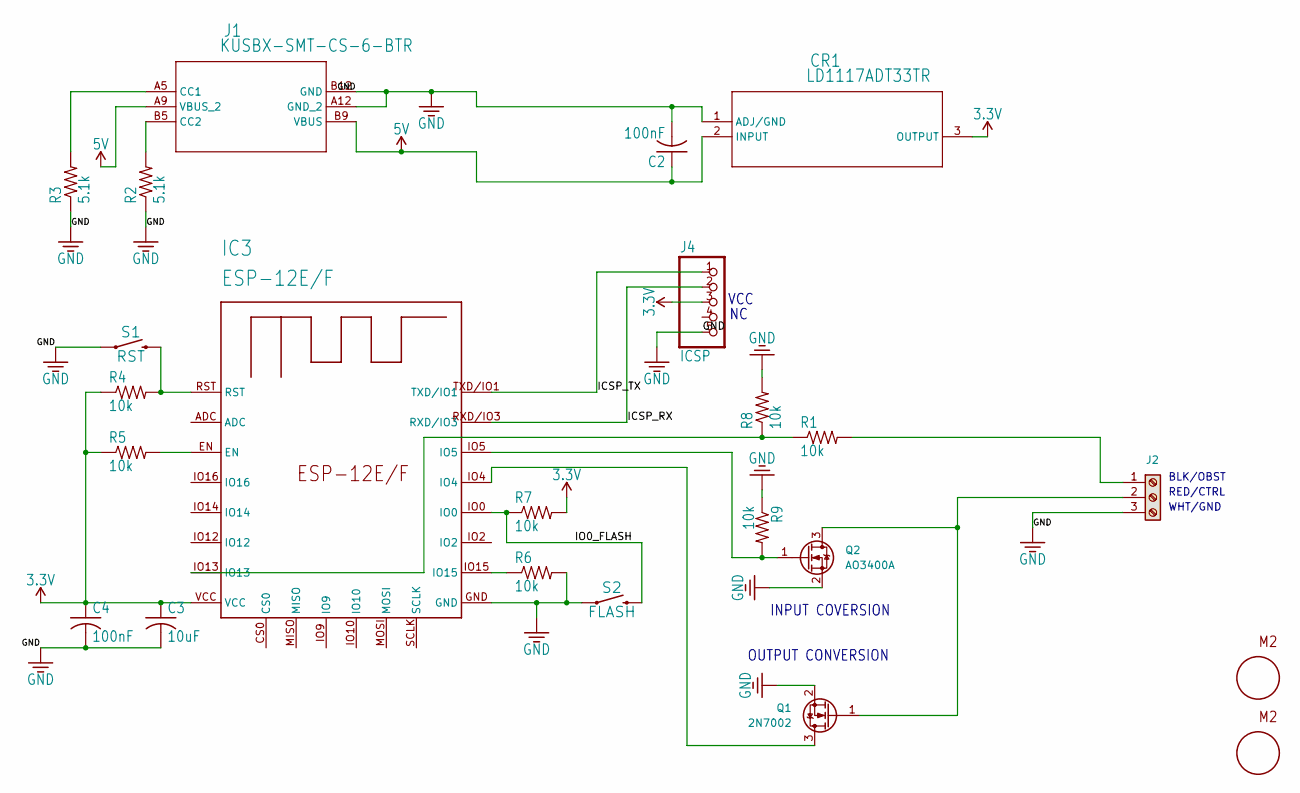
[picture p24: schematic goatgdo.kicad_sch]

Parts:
C2, C4: 100nF; C0805
C3: 10uF; C0805
CR1: LD1117ADT33TR; DPAK_STM
IC3: ESP-12E/F; ESP-12E
J1: KUSBX-SMT-CS-6-BTR; KUSBX-SMT-CS-6-BTR_KYC
J2: Screw_Terminal_01x03; TerminalBlock_MetzConnect_Type011_RT05503HBWC_1x03_P5.00mm_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
J4: ICSP; 1X05
Q1: 2N7002; SOT-23_Handsoldering
Q2: AO3400A; SOT-23_Handsoldering
R1, R4, R5, R6, R7, R8, R9: 10k; R0805
R2, R3: 5.1k; R0805
S1: RST; TACTILE_SWITCH_PTH_6.0MM
S2: FLASH; TACTILE_SWITCH_PTH_6.0MM
U$4, U$6: M2-POST

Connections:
3.3V: C3.1, C4.1, CR1.3 (OUTPUT), IC3.VCC, J4.3, R4.1, R5.1, R7.2
5V: C2.1, CR1.2 (INPUT), J1.A9 (VBUS_2), J1.B9 (VBUS)
/ICSP_RX: IC3.RXD/IO3, J4.2
/ICSP_TX: IC3.TXD/IO1, J4.1
/IO0_FLASH: IC3.IO0, R7.1, S2.3 (2)
GND: C2.2, C3.2, C4.2, CR1.1 (ADJ/GND), IC3.GND, J1.A12 (GND_2), J1.B12 (GND), J2.3, J4.5, Q1.2 (S), Q2.2 (S), R2.1, R3.1, R6.2, R8.2, R9.1, S1.1, S2.1
unnamed: IC3.EN, R5.2
unnamed: IC3.IO13, R1.1, R8.1
unnamed: IC3.IO15, R6.1
unnamed: J1.A5 (CC1), R3.2
unnamed: J1.B5 (CC2), R2.2
unnamed: J2.1, R1.2
unnamed: J2.2, Q1.1 (G), Q2.3 (D)
unnamed: IC3.IO4, Q1.3 (D)
unnamed: IC3.IO5, Q2.1 (G), R9.2
unnamed: IC3.RST, R4.2, S1.3 (2)

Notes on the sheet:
INPUT COVERSION
BLK/OBST
WHT/GND
OUTPUT CONVERSION
RED/CTRL
VCC

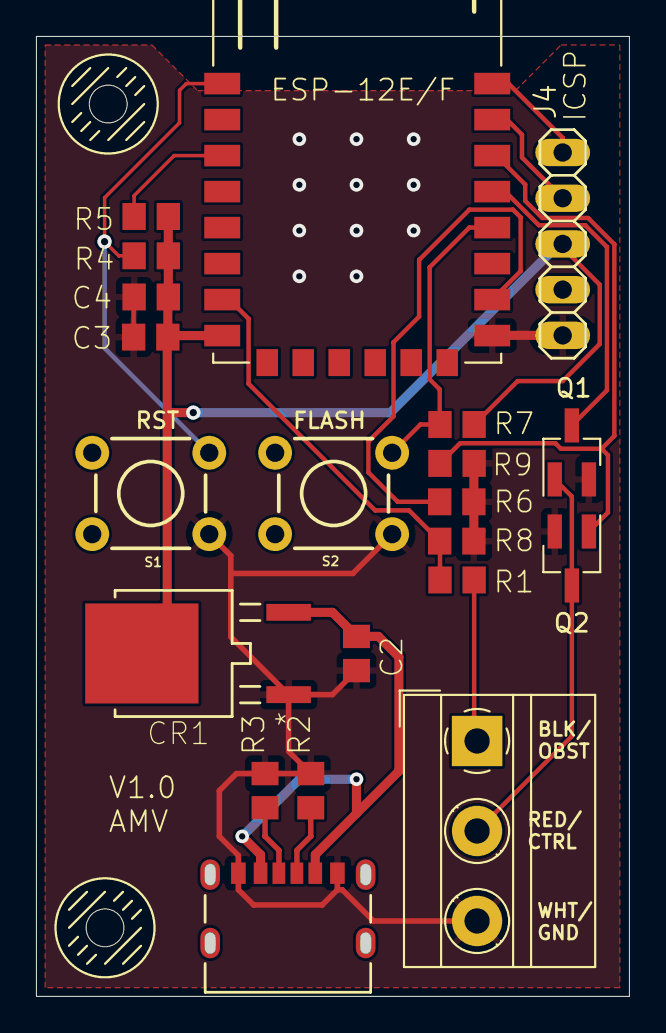
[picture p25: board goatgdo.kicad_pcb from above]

Board: 2 copper layers, 32.9 x 53.3 mm, 23 parts (0 on the bottom side), 16 nets.

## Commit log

2023-10-25 Better MOSFET recommendations
    Due to switching voltage of ESP8266 (3.3v) the IRLB8721 is a better recommendation when using through-hole designs.
2023-10-25 Updated schematic using IRLB8721 MOSFET for TX
    TX should use a MOSFET which will more reliably switch with 3.3v logic.
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2023-10-25 v3 Diagram as Fritzing has S/G/G wrong
    MOSFET layout for Source/Gate/Drain in Fritzing is apparently wrong. Adding S/G/D labels for clarity.
2023-10-25 Updated diagram to v3
    Fritzing appears to be stuffing up the Source/Gate/Drain pin numbering of MOSFET icons so we added S/G/D labels.
2023-10-25 Delete ratgdo open source_schem.png
    Removed due to recommendation of MOSFETs wrong.
2023-10-25 Added notes about why we use D1
    D1 (GPIO5) is used for TX as per ratgdo v2.5 boards which the ESPHome version is now using for flashing.
2023-10-25 Confirmed this design is using code for board rev 2.5
    As of ratgdo board revision 2.5 the code now uses D1 (GPIO5) for TX. This PCB design expected to use that code.
2023-10-25 Clarified which installers to use
    ESPHome Web installer allows for installation to v1.0, 2.0 and v2.5 boards. The schematic shown is based on the v2.5 board layout. Use of Paul Wieland's installer only supports v2.0 boards currently 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
2023-10-25 Replaced diagrams with Ki-Cad version
    No longer using Baby's First PCB Fesigner (aka Fritzing).
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2023-10-25 Ki-cad file was wrong.
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2023-10-26 Added 10k resistor to Obst. circuit as this is a voltage divider
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2023-10-26 Fixed stupid wire routing in diagram
    Diagram v5 had the Drain of the TX MOSFET connected to Ground rather than the Red Wire.
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2023-10-28 v6 diagram still had stupid Fritzing GND routing wrong.
2023-10-28 Delete original breadboard image
    Breadboard original image missing 10k resistor on obstruction wire for voltage divider.
2023-10-28 Adding KiCAD Files and gerber files for review.
    [RatGDO-OpenSource-B_Cu.gbl, RatGDO-OpenSource-B_Cu.gbr, RatGDO-OpenSource-B_Mask.gbr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]
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2023-10-28 Updated Files to match new Schematics
    [RatGDO-OpenSource-B_Cu.gbl, RatGDO-OpenSource-B_Mask.gbs, RatGDO-OpenSource-B_Paste.gbp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]
2023-10-29 Remove power supply components
    [RatGDO-OpenSource-B_Cu.gbl, RatGDO-OpenSource-B_Mask.gbs, RatGDO-OpenSource-B_Paste.gbp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]
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2023-10-31 Redid folder structure and setup folders for different modules
    Redid folder structure
    Added folders and projects for D1 minis in the ESP32 and ESP8266 varieties
    [RatGDO-OpenSource-D1Mini-ESP32-B_Cu.gbl, RatGDO-OpenSource-D1Mini-ESP32-B_Cu.gbr, RatGDO-OpenSource-D1Mini-ESP32-B_Mask.gbr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]
2023-10-31 Handling Merge conflicts
    [RatGDO-OpenSource-D1Mini-ESP32-B_Cu.gbl, RatGDO-OpenSource-D1Mini-ESP32-B_Mask.gbs, RatGDO-OpenSource-D1Mini-ESP32-B_Paste.gbp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]
2023-10-31 Forcing old files to delete
    [RatGDO-OpenSource-B_Cu.gbl, RatGDO-OpenSource-B_Cu.gbr, RatGDO-OpenSource-B_Mask.gbr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]
2023-10-31 Fixed Bad PCB Labeling
    [RatGDO-OpenSource-D1Mini-ESP32-B_Cu.gbl, RatGDO-OpenSource-D1Mini-ESP32-B_Mask.gbs, RatGDO-OpenSource-D1Mini-ESP32-B_Paste.gbp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]
2023-10-31 Force Recreate of Gerber files
    [RatGDO-OpenSource-D1Mini-ESP32-B_Cu.gbl, RatGDO-OpenSource-D1Mini-ESP32-B_Cu.gbr, RatGDO-OpenSource-D1Mini-ESP32-B_Mask.gbr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]
2023-10-31 Change Pin Header to Pin Socket
    [RatGDO-OpenSource-D1Mini-ESP32-B_Cu.gbl, RatGDO-OpenSource-D1Mini-ESP32-B_Mask.gbs, RatGDO-OpenSource-D1Mini-ESP32-B_Paste.gbp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]
2023-10-31 Cleaning up Schematics and making PCB layout similar for D1 Boards
    [RatGDO-OpenSource-D1Mini-ESP32-B_Cu.gbl, RatGDO-OpenSource-D1Mini-ESP32-B_Mask.gbs, RatGDO-OpenSource-D1Mini-ESP32-B_Paste.gbp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]
2023-10-31 Updating BOM Files for D1 Mini-8266
    [RatGDO-OpenSource-D1Mini-ESP8266-B_Cu.gbl, RatGDO-OpenSource-D1Mini-ESP8266-B_Mask.gbs, RatGDO-OpenSource-D1Mini-ESP8266-B_Paste.gbp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]
2023-11-01 Replaced image with schematic using RFP30N06LE
    Removal of IRLB8721 and replacement with RFP30N06LE.
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2023-11-07 Added Bare ESP8266 kicad files.
    [RatGDO-OpenSource-Bare-ESP8266-B_Cu.gbl, RatGDO-OpenSource-Bare-ESP8266-B_Mask.gbs, RatGDO-OpenSource-Bare-ESP8266-B_Paste.gbp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]
2023-11-08 Missed Silkscreening for programming header
    [RatGDO-OpenSource-Bare-ESP8266-B_Cu.gbl, RatGDO-OpenSource-Bare-ESP8266-B_Mask.gbs, RatGDO-OpenSource-Bare-ESP8266-B_Paste.gbp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]
2023-11-08 Updated Trace widths
    [RatGDO-OpenSource-Bare-ESP8266-B_Cu.gbl, RatGDO-OpenSource-Bare-ESP8266-B_Mask.gbs, RatGDO-OpenSource-Bare-ESP8266-B_Paste.gbp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]
2023-11-08 Added silkscreen to LM2596 area to aid in placement.
    [RatGDO-OpenSource-Bare-ESP8266-B_Cu.gbl, RatGDO-OpenSource-Bare-ESP8266-B_Mask.gbs, RatGDO-OpenSource-Bare-ESP8266-B_Paste.gbp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]
2023-11-10 ESP32 footprint did not properly create a keepout zone.
    [RatGDO-OpenSource-D1Mini-ESP32-B_Cu.gbl, RatGDO-OpenSource-D1Mini-ESP32-B_Mask.gbs, RatGDO-OpenSource-D1Mini-ESP32-B_Paste.gbp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]
2023-11-10 ESP8266 footprint did not properly create a keepout zone.
    [RatGDO-OpenSource-D1Mini-ESP8266-B_Cu.gbl, RatGDO-OpenSource-D1Mini-ESP8266-B_Mask.gbs, RatGDO-OpenSource-D1Mini-ESP8266-B_Paste.gbp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]
2023-11-11 Add new wide board format for D1 Mini ESP32
    [RatGDO-OpenSource-D1Mini-ESP32.kicad_pcb, RatGDO-OpenSource-D1Mini-ESP32.kicad_sch]
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2023-11-14 Cleanup files for gerber builds
    [RatGDO-OpenSource-Bare-ESP8266-B_Cu.gbl, RatGDO-OpenSource-Bare-ESP8266-B_Mask.gbs, RatGDO-OpenSource-Bare-ESP8266-B_Paste.gbp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]
2023-11-17 Fixed Silkscreen issue - positive and ground swap
    [RatGDO-OpenSource-Bare-ESP8266.kicad_pcb, RatGDO-OpenSource-D1Mini-ESP32.csv, RatGDO-OpenSource-D1Mini-ESP32.kicad_pcb]
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2023-11-24 Replaced Fritzing Schematic
2023-11-24 Update ESP8266 schematics and PCB
    Added 1K R4 on gate of Q2.
    Added 10K R5/R6 on gate of Q1.
    Re-laid out PCB, all single sided and smaller.
    [RatGDO-OpenSource-D1Mini-ESP8266.kicad_pcb, RatGDO-OpenSource-D1Mini-ESP8266.kicad_sch]
2023-11-24 Update ESP32 Mini schematics and PCB
    Changed pads to hand solder.
    Modified from ESP8266 layout.
    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
    [RatGDO-OpenSource-D1Mini-ESP32.kicad_pcb, RatGDO-OpenSource-D1Mini-ESP32.kicad_sch]
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2024-01-11 Added KiCad Project
    [goatgdo.kicad_pcb, goatgdo.kicad_sch]
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2024-03-19 Update schematics for mini wide board v2.5
    [RatGDO-OpenSource-Bare-ESP8266.kicad_pcb, RatGDO-OpenSource-D1Mini-ESP32.kicad_pcb, RatGDO-OpenSource-D1Mini-ESP32.kicad_sch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]
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
